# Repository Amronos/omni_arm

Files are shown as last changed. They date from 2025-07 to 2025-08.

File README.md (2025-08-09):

# Omni Arm

**_This is a work in progress and not usable currently._**

A universal robot arm featuring 3 robot grippers (parallel jaw, suction cup, and jamming) and 9 DOFS (including 3 for each gripper), allowing it to pickup objects of any kind as long as they have reasonable size and weight.

## Features

- 1 DOF for rotation on the x-axis.
- 3 DOFs for rotation on the y-axis.
- 2 DOFs for rotation on the z-axis.
- 3 different grippers: parallel jaw, suction cup, and jamming.
- Can pickup objects of any kind as long as they are of reasonable weight and size (size is not a limit for the suction cup gripper).
- Precise arm position control alongside position, velocity, load, and input voltage feedback from Waveshare servo motors.
- [ROS 2](https://docs.ros.org) support that uses [MoveIt 2](https://moveit.ai). (Coming Soon)

## Why Create This?

There are hardly any open-source and low-cost robot arms available out there that allow you to pikcup all sorts of objects with the use of various grippers.<br>
Most of the avilable robot arms also don't offer the kind of feedback and control one needs on the motors to perform complex kinematics and dynamics.<br>
This robot arm does all of that, making it perfect for my use-cases.

## Images

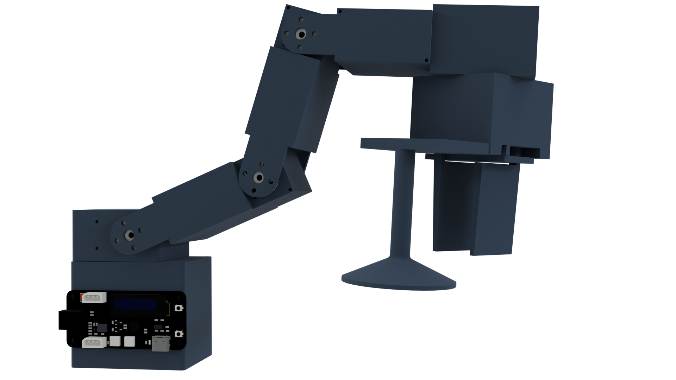
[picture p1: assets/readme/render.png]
Render

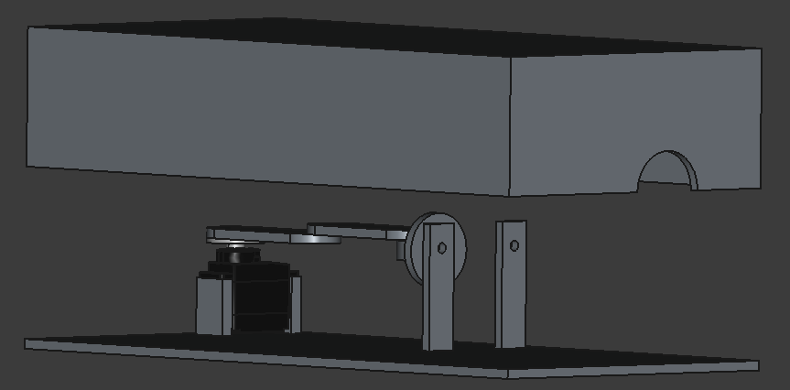
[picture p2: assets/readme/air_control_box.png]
Air Control Box

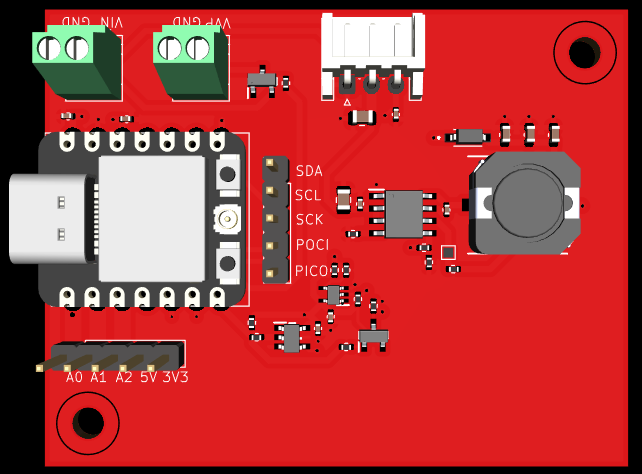
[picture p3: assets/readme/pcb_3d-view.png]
PCB 3D View


## Wiring Diagram

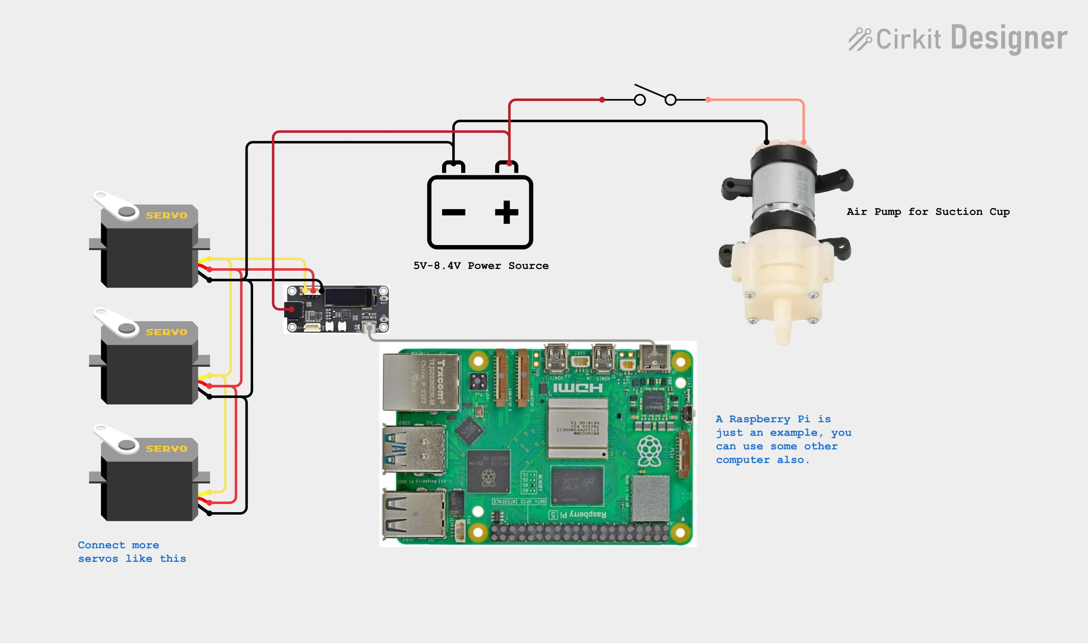
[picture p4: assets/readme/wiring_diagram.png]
Wiring Diagram


## BOM

| Item | Unit Price | Quantity | Total Price | Links |
| --- | --- | --- | --- | --- |
| Waveshare SC15 Servo | $17.99 | 4 | $71.96 | https://www.waveshare.com/sc15-servo.htm |
| Waveshare SC09 Servo | $8.99 | 4 | $35.96 | https://www.waveshare.com/sc09-servo.htm |
| PCB | $43.77 | 2 | $43.77 | https://jlpcb.com/ |
| Xiao ESP32-C3 | $5.71 | 1 | $5.71 | https://thinkrobotics.com/products/seeed-studio-xiao-esp32c3 |
| Dispo Van 20 ml Plastic Syringe | $0.23 | 1 | $0.23 | https://www.amazon.in/DISPO-Plastic-Syringe-Medical-Purpose/dp/B09KS18BMY |
| Suction Cup Gripper for DIY Robot Arms  | $27.85 | 1 | $27.85 | https://thinkrobotics.com/products/suction-cup-gripper-for-diy-robot-arms |
| M2x9.5 Pan Head Self Tapping Screw | — | 10 | — | — |
| M2x6.5 Pan Head Self Tapping Screw | — | 10 | — | — |
| M3x8 Pan Head Self Tapping Screw | — | 4 | — | — |
| M3x10 Pan Head Self Tapping Screw | — | 2 | — | — |
| 2x50mm Stainless Steel Round Shaft Rods | — | 2 | — | — |
| 3D Prints | — | 1 | — | https://github.com/Amronos/omni_arm/tree/main/CAD |
| | | | $185.48 | |

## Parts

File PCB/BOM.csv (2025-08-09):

Designator | Quantity | Value | Footprint | Manufacturer | Mfr. Part No. | JLCPCB Part #
C1, C12 | 2 | 10 µF | C_0805_2012Metric | Murata Electronics | GRM21BR61H106KE43L | C440198
C10, C2, C3, C7, C8, C9 | 6 | 100 nF | C_0402_1005Metric | Samsung Electro-Mechanics | CL05B104KB54PNC | C307331
C11 | 1 | 470 pF | C_0402_1005Metric | Murata Electronics | GCM155R72A471KA37D | C464449
C4, C5, C6 | 3 | 22 µF | C_0603_1608Metric | Murata Electronics | GRT188R61A226ME13D | C126630
D1 | 1 | 1N5819HW-7-F | SOD3715X145N | Diodes Incorporated | 1N5819HW-7-F | C82544
J1, J4 | 2 | Screw_Terminal_01x02 | TerminalBlock_Xinya_XY308-2.54-2P_1x02_P2.54mm_Horizontal | Ningbo Xinlaiya Elec. | XY308-2.54-2P | C557685
J2, J3 | 2 | Conn_01x05 | PinHeader_1x05_P2.54mm_Vertical | Generic | Generic
J5 | 1 | Conn_01x03 | JST_EH_S3B-EH_1x03_P2.50mm_Horizontal | BOOMELE(Boom Precision Elec) | 5264-3A | C146133
L1 | 1 | 15 µH | INDPM102100X400N | Coilcraft | MSS1038-153MLC | C18212714
Q1, Q2 | 2 | MMBT3906LT3G | SOT96P237X111-3N | Onsemi | MMBT3906LT3G | C232602
R1, R10, R11, R13, R3, R4, R9 | 7 | 10 kΩ | R_0402_1005Metric | Panasonic Electronic Components | ERA-2AEB103X | C191915
R6 | 1 | 64.9 kΩ | R_0402_1005Metric | Panasonic Electronic Components | ERA-2AEB6492X | C490835
R7 | 1 | 100 kΩ | R_0402_1005Metric | Panasonic Electronic Components | ERA-2AEB104X | C445619
R8 | 1 | 24.9 kΩ | R_0402_1005Metric | Panasonic Electronic Components | ERA-2AEB2492X | C490822
U1 | 1 | MOUDLE-SEEEDUINO-XIAO-ESP32C3 | XIAO-ESP32C3-SMD | Seeed Studio | XIAO ESP32C3
U3 | 1 | LMR38020FDDAR | SOIC127P600X170-9N | Texas Instruments | LMR38020FDDAR | C5149193
U4 | 1 | SN74LVC1G126DBVR | SOT95P280X145-5N | Texas Instruments | SN74LVC1G126DBVR | C7834
U5 | 1 | SN74LVC1G125DCKR | SOT65P210X110-5N | Texas Instruments | SN74LVC1G125DCKR | C7833

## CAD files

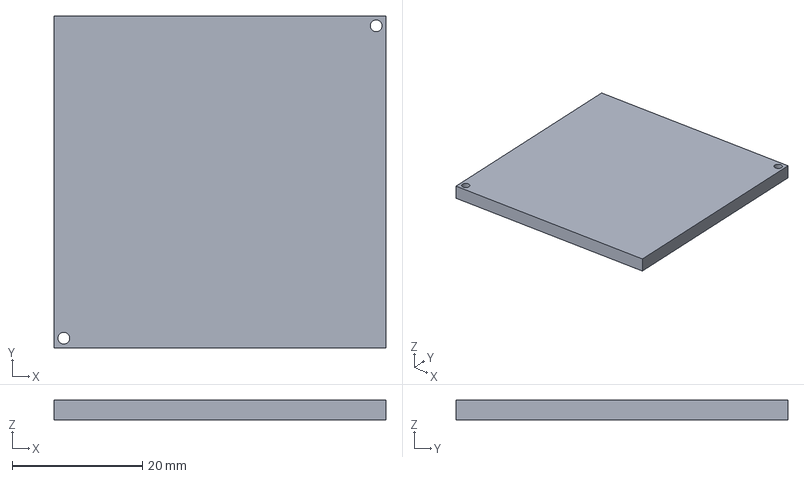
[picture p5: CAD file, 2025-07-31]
CAD/Z-Axis_2_Front.step
50.9 x 50.9 x 3.00 mm

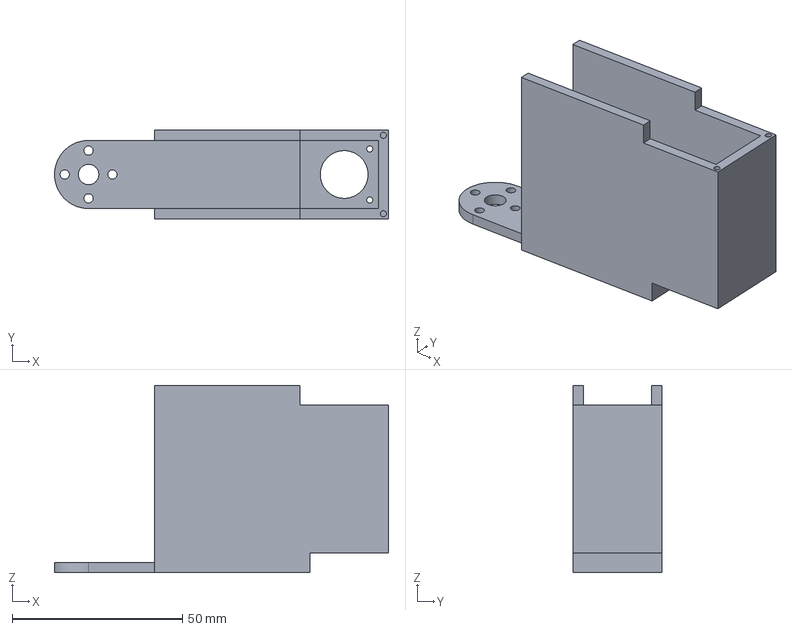
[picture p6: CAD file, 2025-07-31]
CAD/Y-Axis_2_Left.step
98.0 x 26.0 x 54.9 mm

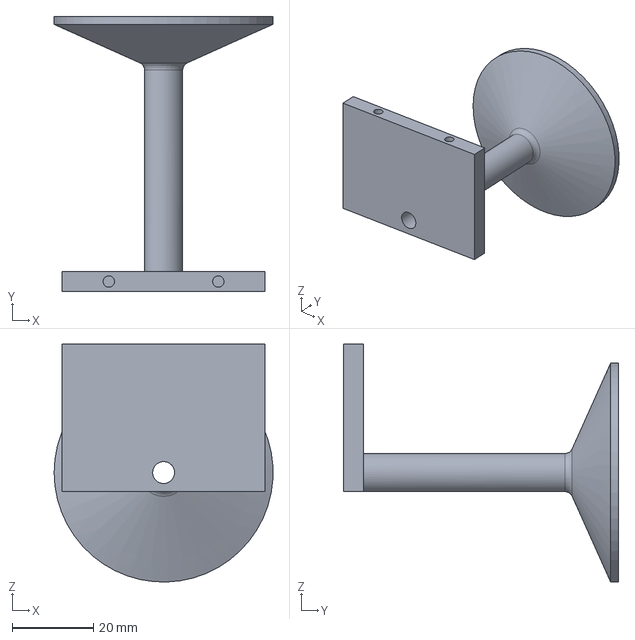
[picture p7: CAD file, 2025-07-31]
CAD/Jamming_Gripper_Funnel.step
53.9 x 67.9 x 58.7 mm

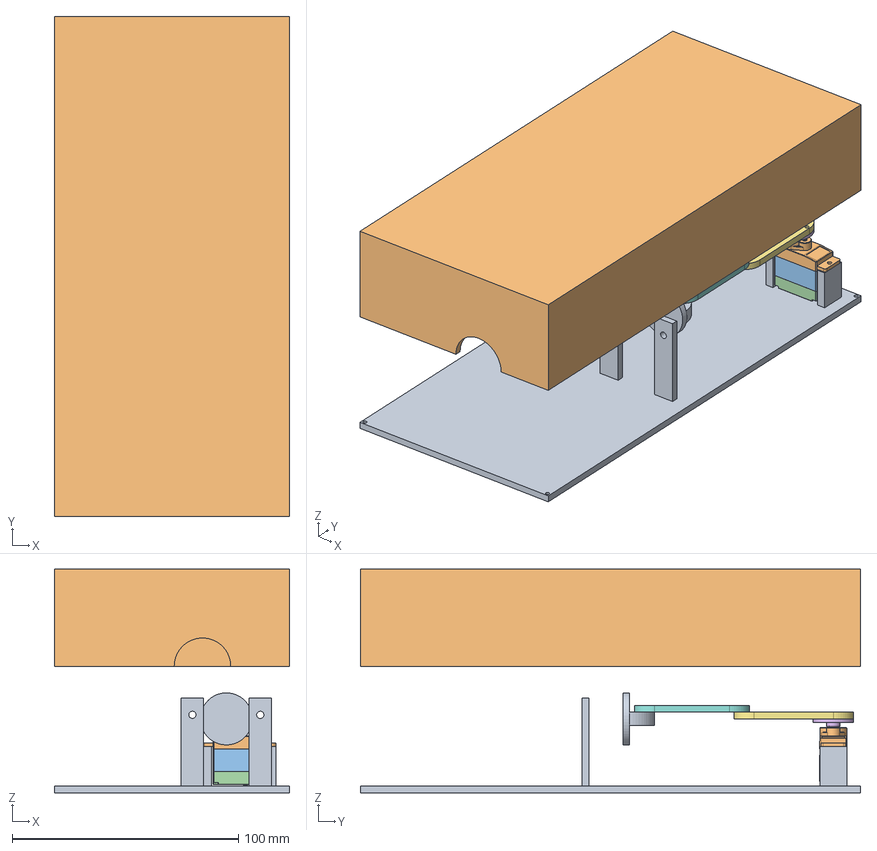
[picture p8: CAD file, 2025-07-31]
CAD/air_control_box.FCStd
104.0 x 221.0 x 99.0 mm
Base
SJ-WK00-0038-TOPCASE-0716_41_1
SJ-WK00-0039-COREMIDDLE-0716_65
SJ-WK00-0037-BOTTOMCASE-0716_9_
SJ-CL00-0027-OUTPUTGEAR-0716_37
SC09_Horn
Syringe_Connector
Cover

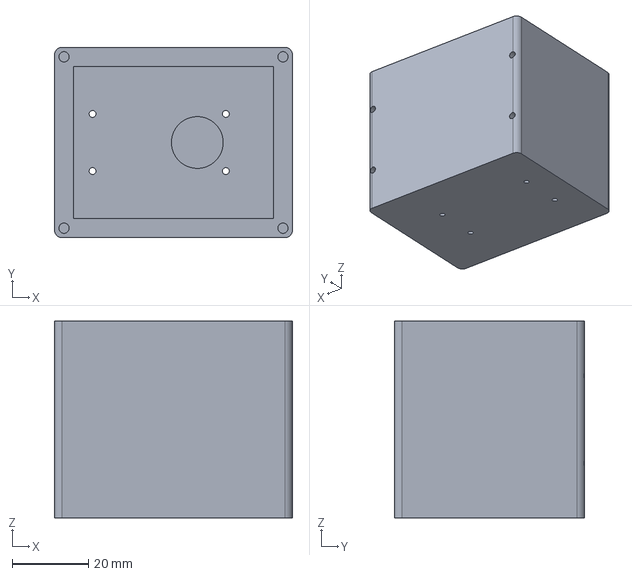
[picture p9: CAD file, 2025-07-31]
CAD/Z-Axis_Base.step
62.5 x 50.0 x 51.7 mm

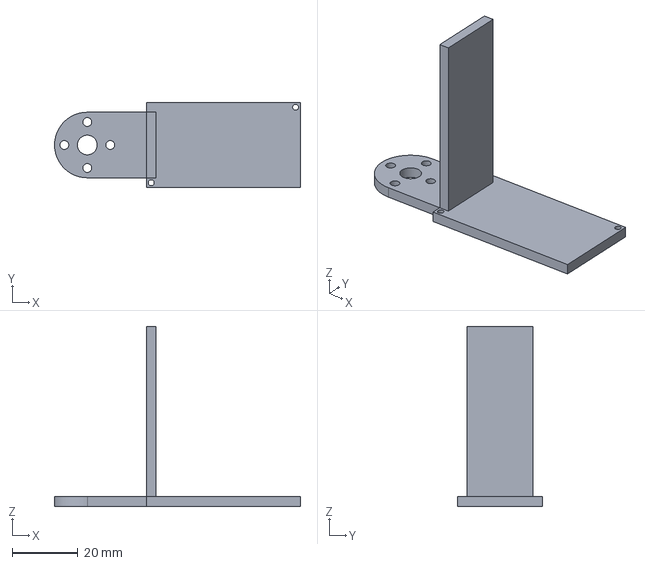
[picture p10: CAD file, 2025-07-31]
CAD/X-Axis_Right.step
75.0 x 26.0 x 54.9 mm

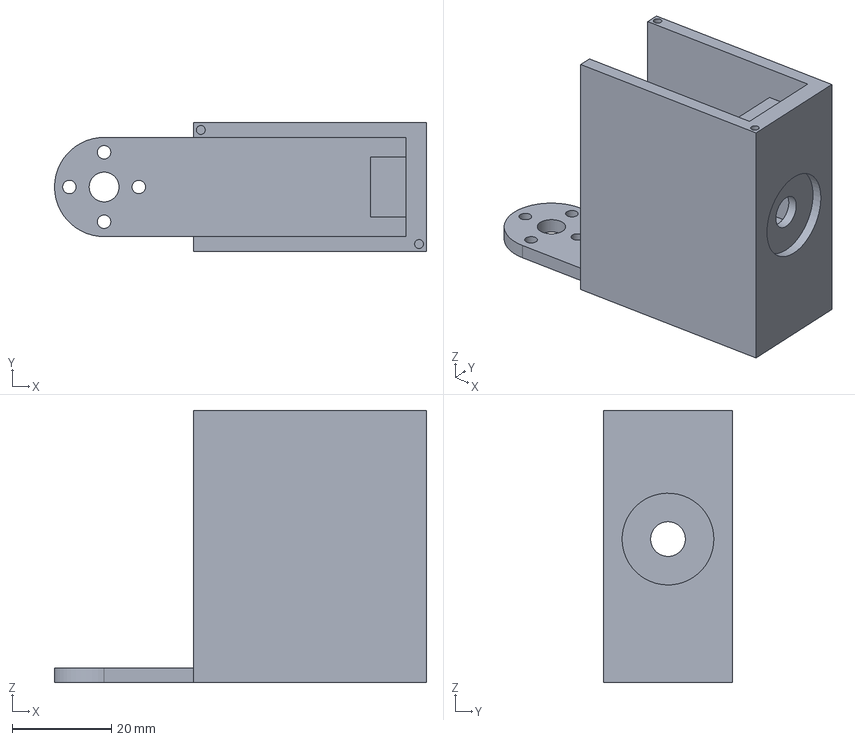
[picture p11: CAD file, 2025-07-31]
CAD/X-Axis_Left.step
75.0 x 26.0 x 54.9 mm

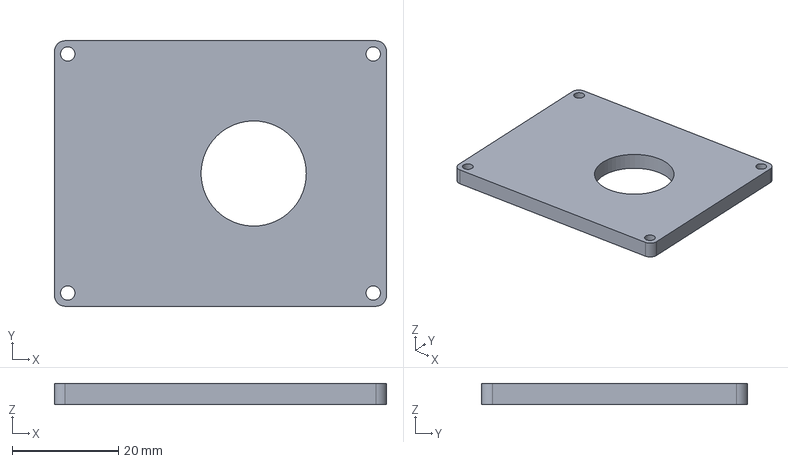
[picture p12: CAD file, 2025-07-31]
CAD/Z-Axis_Lid.step
62.5 x 50.0 x 3.98 mm

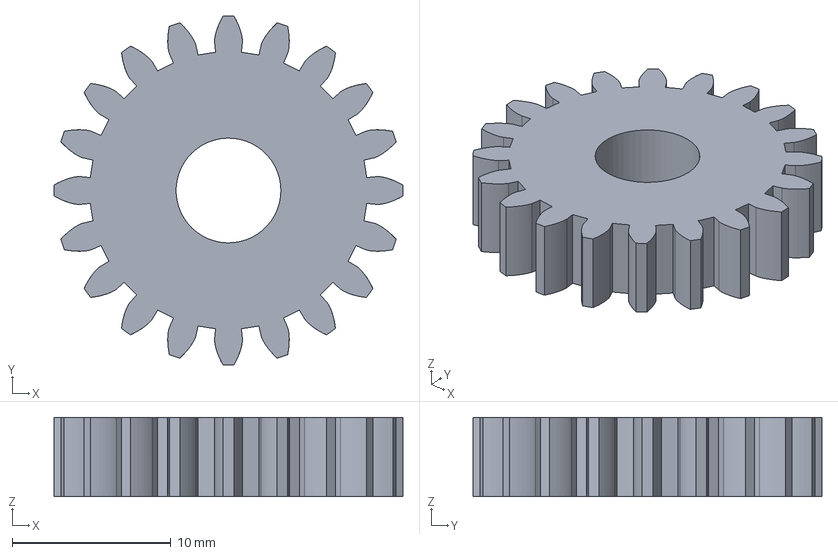
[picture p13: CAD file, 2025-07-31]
CAD/Parallel_Gripper_Part_3.step
22.0 x 22.0 x 5.00 mm

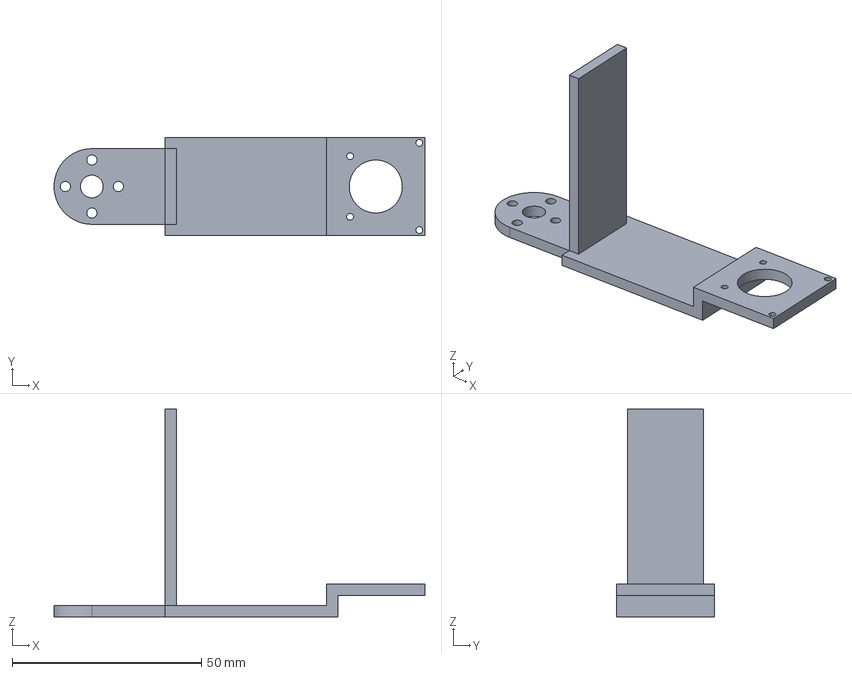
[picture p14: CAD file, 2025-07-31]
CAD/Y-Axis_2_Right.step
98.0 x 26.0 x 54.9 mm

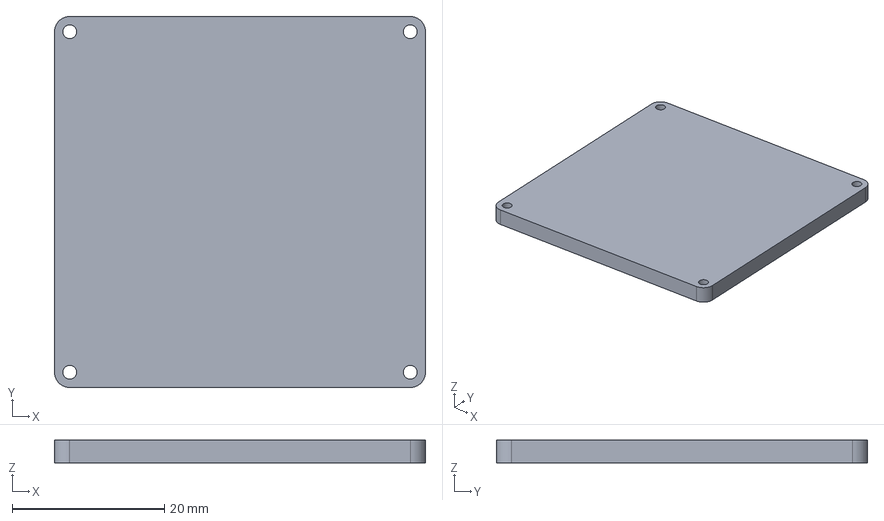
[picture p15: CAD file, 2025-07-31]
CAD/Y-Axis_Lid.step
48.7 x 48.7 x 3.00 mm

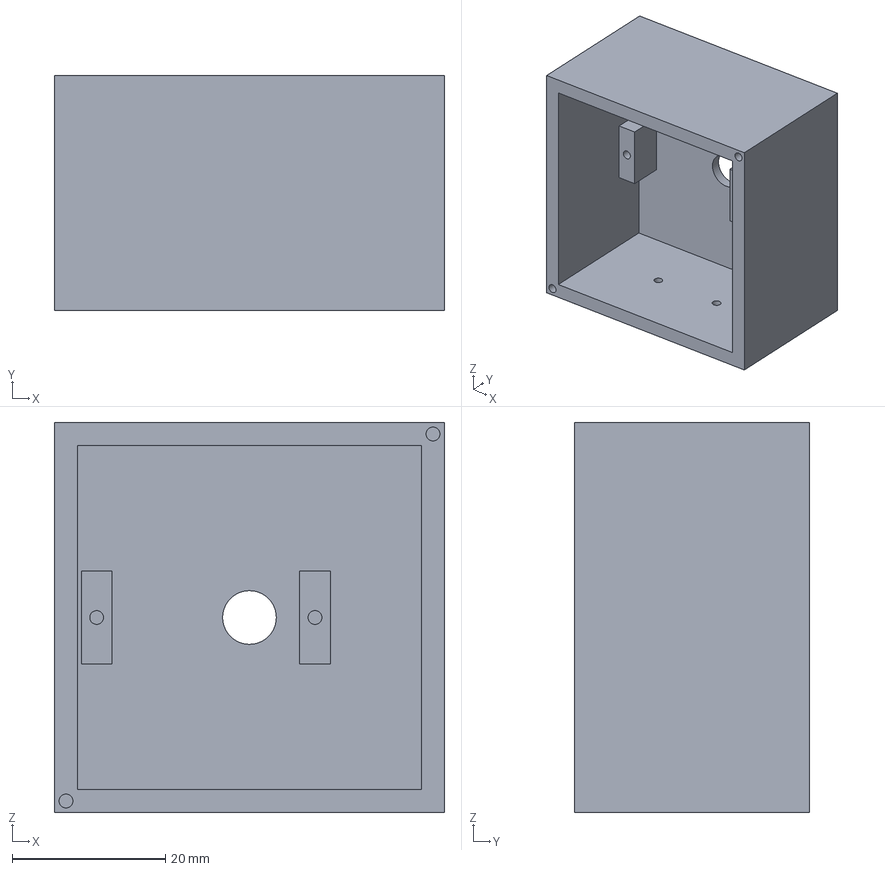
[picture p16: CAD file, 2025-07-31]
CAD/Z-Axis_2_Back.step
50.9 x 30.6 x 50.9 mm

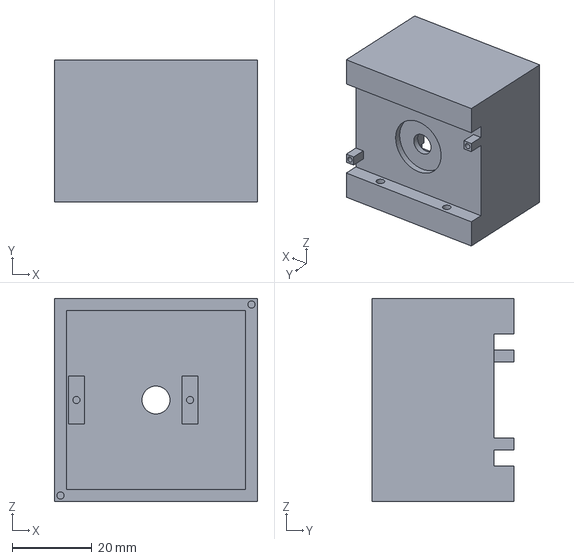
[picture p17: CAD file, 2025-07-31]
CAD/Parallel_Gripper_Part_1.step
50.9 x 35.6 x 50.9 mm

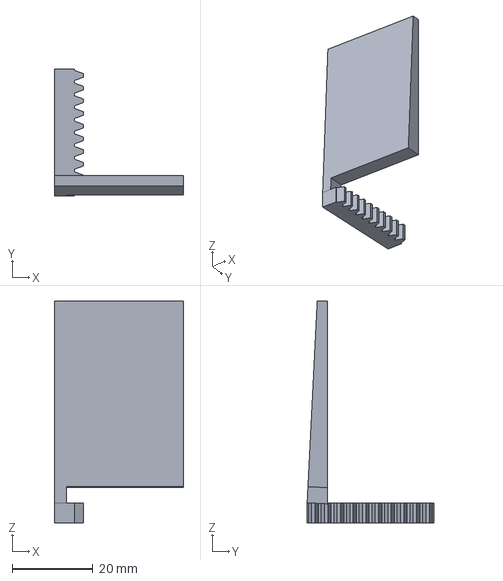
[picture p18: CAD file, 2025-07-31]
CAD/Parallel_Gripper_Part_4.step
32.0 x 31.4 x 55.0 mm

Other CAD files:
CAD/Parallel_Gripper_Part_2.step
CAD/Parallel_Gripper_Part_5.step
CAD/Y-Axis_Base.step
CAD/omni_arm.FCStd

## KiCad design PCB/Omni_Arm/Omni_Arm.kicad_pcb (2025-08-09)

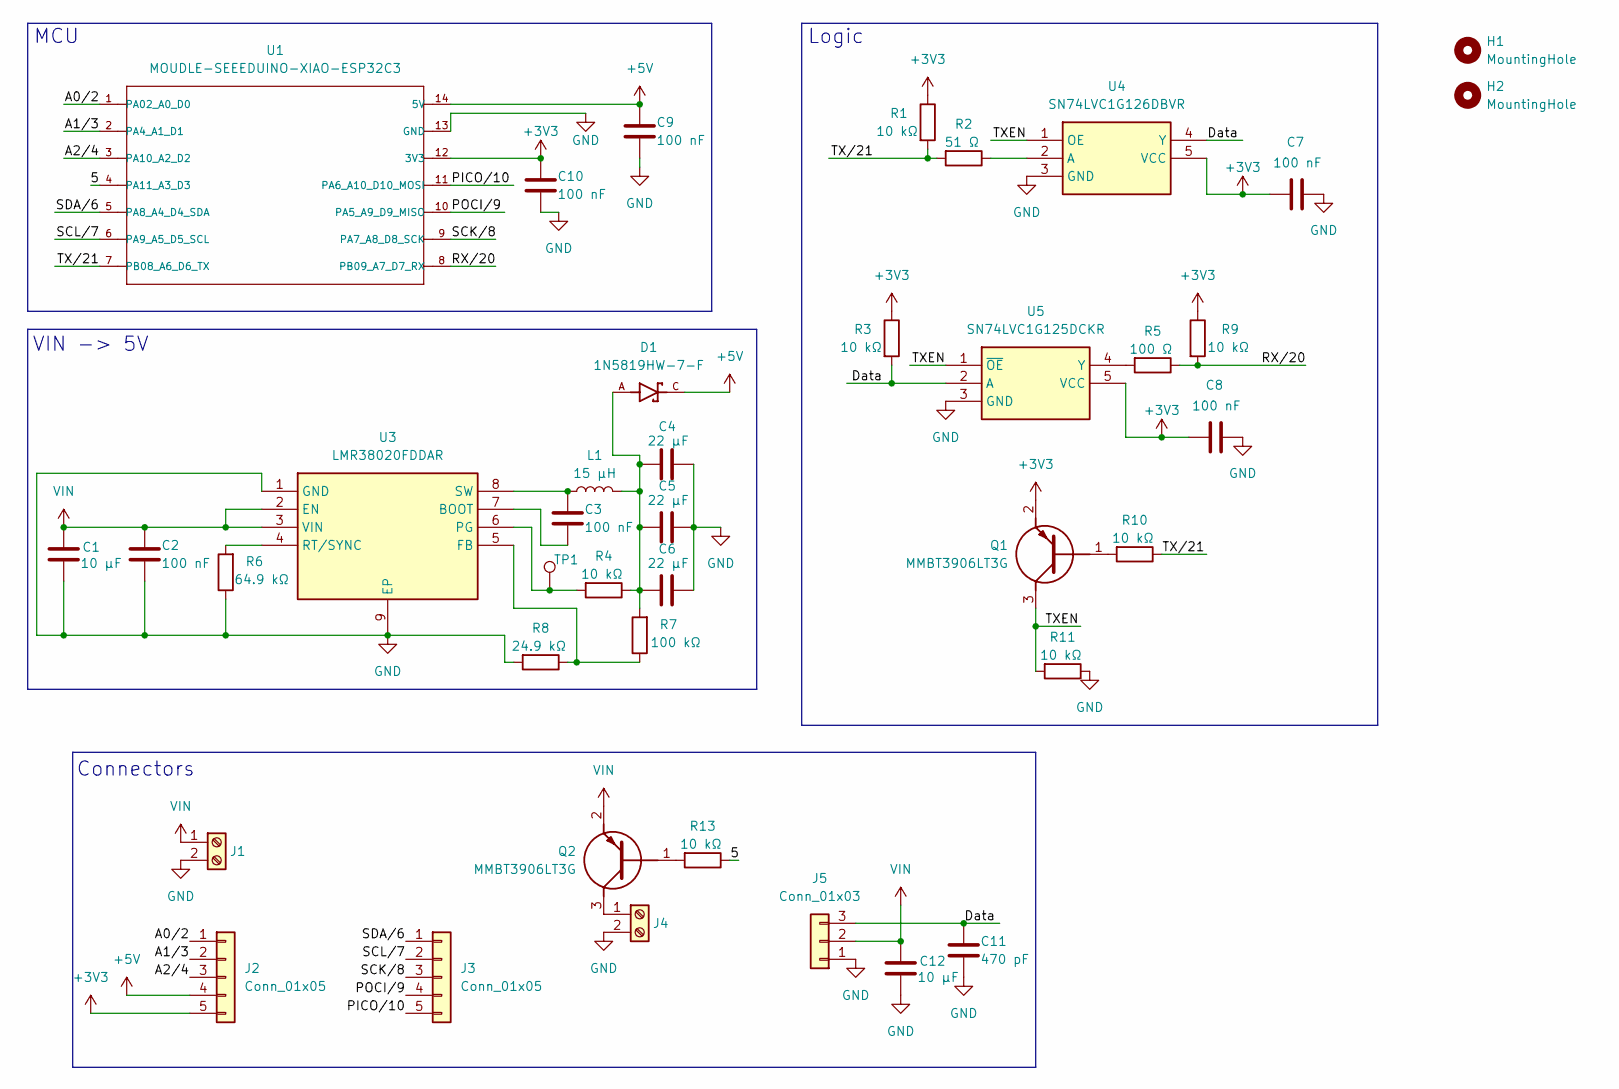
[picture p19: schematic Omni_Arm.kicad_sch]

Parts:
C1, C12: 10 µF; C_0805_2012Metric
C2, C3, C7, C8, C9, C10: 100 nF; C_0402_1005Metric
C4, C5, C6: 22 µF; C_0603_1608Metric
C11: 470 pF; C_0402_1005Metric
D1: 1N5819HW-7-F; SOD3715X145N
H1, H2: MountingHole; MountingHole_3.2mm_M3
J1, J4: Screw_Terminal_01x02; TerminalBlock_Xinya_XY308-2.54-2P_1x02_P2.54mm_Horizontal
J2, J3: Conn_01x05; PinHeader_1x05_P2.54mm_Vertical
J5: Conn_01x03; JST_EH_S3B-EH_1x03_P2.50mm_Horizontal
L1: 15 µH; INDPM102100X400N
Q1, Q2: MMBT3906LT3G; SOT96P237X111-3N; Mouser Part Number 863-MMBT3906LT3G
R1, R3, R4, R9, R10, R11, R13: 10 kΩ; R_0402_1005Metric
R2: 51 Ω; R_0402_1005Metric
R5: 100 Ω; R_0402_1005Metric
R6: 64.9 kΩ; R_0402_1005Metric
R7: 100 kΩ; R_0402_1005Metric
R8: 24.9 kΩ; R_0402_1005Metric
TP1: TestPoint; TestPoint_Pad_1.0x1.0mm
U1: MOUDLE-SEEEDUINO-XIAO-ESP32C3; XIAO-ESP32C3-SMD
U3: LMR38020FDDAR; SOIC127P600X170-9N
U4: SN74LVC1G126DBVR; SOT95P280X145-5N; Manufacturer_Part_Number SN74LVC1G126DBVR; Mouser Part Number 595-SN74LVC1G126DBVR
U5: SN74LVC1G125DCKR; SOT65P210X110-5N; Manufacturer_Part_Number SN74LVC1G125DCKR; Mouser Part Number 595-SN74LVC1G125DCKR

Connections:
+3V3: C7.1, C8.1, C10.1, J2.5, Q1.2 (E), R1.1, R3.1, R9.1, U1.12 (3V3), U4.5 (VCC), U5.5 (VCC)
+5V: C9.1, D1.C, J2.4, U1.14 (5V)
/5: R13.1, U1.4 (PA11_A3_D3)
/A0/2: J2.1, U1.1 (PA02_A0_D0)
/A1/3: J2.2, U1.2 (PA4_A1_D1)
/A2/4: J2.3, U1.3 (PA10_A2_D2)
/Data: C11.1, J5.3, R3.2, U4.4 (Y), U5.2 (A)
/PICO/10: J3.5, U1.11 (PA6_A10_D10_MOSI)
/POCI/9: J3.4, U1.10 (PA5_A9_D9_MISO)
/RX/20: R5.1, R9.2, U1.8 (PB09_A7_D7_RX)
/SCK/8: J3.3, U1.9 (PA7_A8_D8_SCK)
/SCL/7: J3.2, U1.6 (PA9_A5_D5_SCL)
/SDA/6: J3.1, U1.5 (PA8_A4_D4_SDA)
/TXEN: Q1.3 (C), R11.2, U4.1 (OE), U5.1 (~OE)
/TX/21: R1.2, R2.2, R10.1, U1.7 (PB08_A6_D6_TX)
GND: C1.2, C2.2, C4.2, C5.2, C6.2, C7.2, C8.2, C9.2, C10.2, C11.2, C12.2, J1.2, J4.2, J5.1, R6.1, R8.2, R11.1, U1.13 (GND), U3.1 (GND), U3.9 (EP), U4.3 (GND), U5.3 (GND)
unnamed: C4.1, C5.1, C6.1, D1.A, L1.2, R4.1, R7.2
unnamed: J4.1, Q2.3 (C)
unnamed: Q1.1 (B), R10.2
unnamed: Q2.1 (B), R13.2
unnamed: C3.2, U3.7 (BOOT)
unnamed: R7.1, R8.1, U3.5 (FB)
unnamed: R4.2, TP1.1, U3.6 (PG)
unnamed: R6.2, U3.4 (RT/SYNC)
unnamed: C3.1, L1.1, U3.8 (SW)
unnamed: R2.1, U4.2 (A)
unnamed: R5.2, U5.4 (Y)
VIN: C1.1, C2.1, C12.1, J1.1, J5.2, Q2.2 (E), U3.2 (EN), U3.3 (VIN)

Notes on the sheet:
Logic
VIN -> 5V
Connectors
MCU

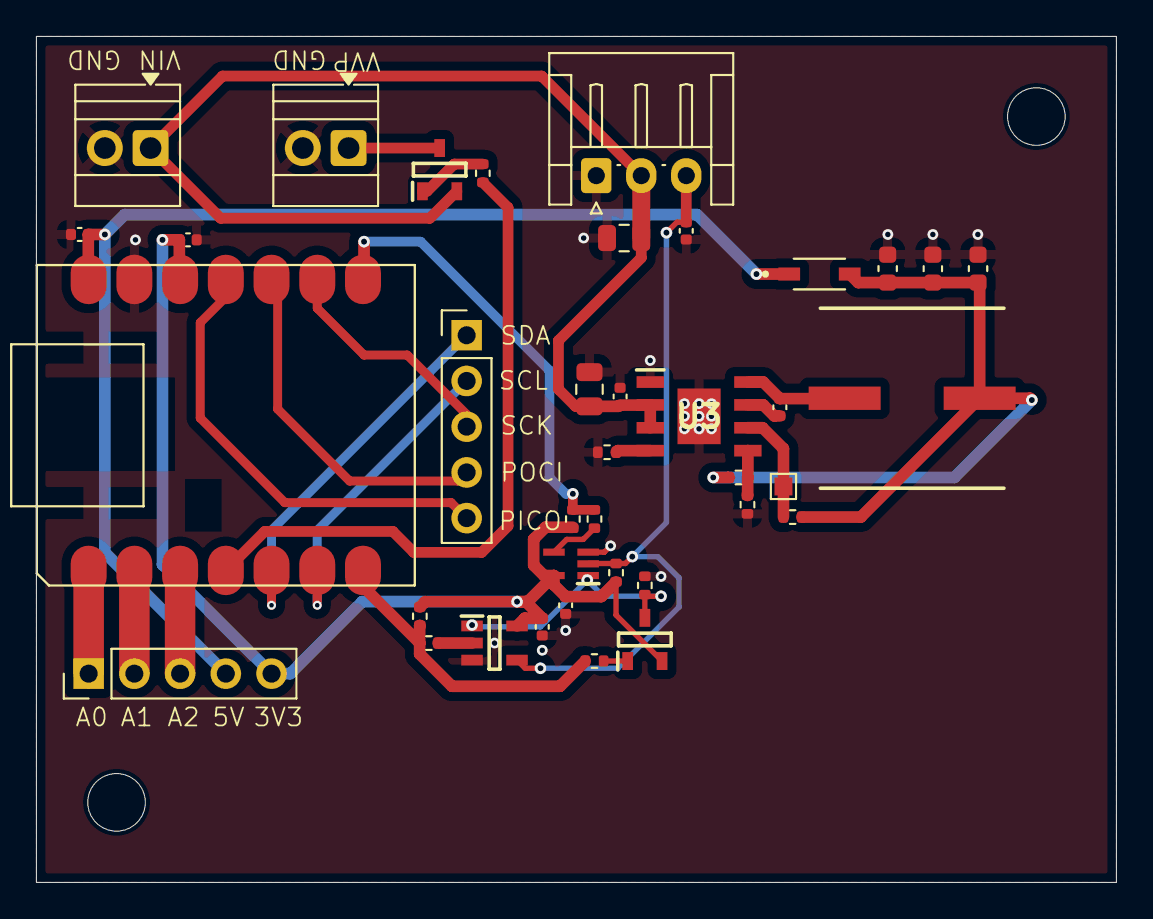
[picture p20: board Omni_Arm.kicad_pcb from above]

Board: 2 copper layers, 60.0 x 47.0 mm, 40 parts (0 on the bottom side), 28 nets.

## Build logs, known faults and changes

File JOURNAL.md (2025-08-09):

---
title: "Omni Arm"
author: "Aarav Gupta"
description: "A unviersal robot arm featuring 3 robot grippers (parallel jaw, suction cup, and jamming) and 9 DOFS."
created_at: "2025-07-8"
total_time_spent: 51 hours
---

## 6th to 8th August 2025: Created a Custom PCB

I still haven't printed the arm, but decided to create a PCB for that so that I can control the suction cup, gripper from the MCU directly, instead of manually operating a switch. (I haven't explicitly mentioned this in the journal before, but this was the case.)<br>
The PCB uses a Xiao ESP32-C3 and can control serial bus servo motors. Therefore, the Waveshare Servo Driver is no longer needed.<br>
To create this PCB I first spent some time looking at commercially availabe serial bus servo motor drivers, after taking inspiration from them I started to design my own.<br>
I then spent some time changing the 3D model of the arm to support the new PCB instead of the previous servo driver, alongside working on the BOM for the PCB and the BOM for the entire project.

| 3D View | Schematic Diagram |
| :---: | :---: |
| 3D View | Schematic Diagram |

**Total time spent: 7h**

## 30th to 31st July 2025: Ready for First Print

I spent these two days completing the jamming gripper and making the air control box (houses the syringe, it's servo motor, and electronics for the suction cup). This project is ready to be printed and tested now!<br>
I haven't made any special mounting for the parts for the suction cup gripper for this first print (I don't know their exact measurements yet), for now they will be hot-glued to the arm / air-control box.<br>
I also completed the first basic version of the firmware and made a wiring diagram.

| Render of the Arm | Air Control Box |
| :---: | :---: |
| Render of the Arm | Air Control Box |

**Total time spent: 10.5h**

## 28th to 29th July 2025: Complete Parallel Gripper

I spent these two days completing the parallel gripper, I used a rack and pinion design for it.<br>
By moving the arm in assembly, I found that the arm would face difficult picking up objects that are near it, when using the suction cup or jamming gripper. To fix this I have added another DOF on the Y-Axis.

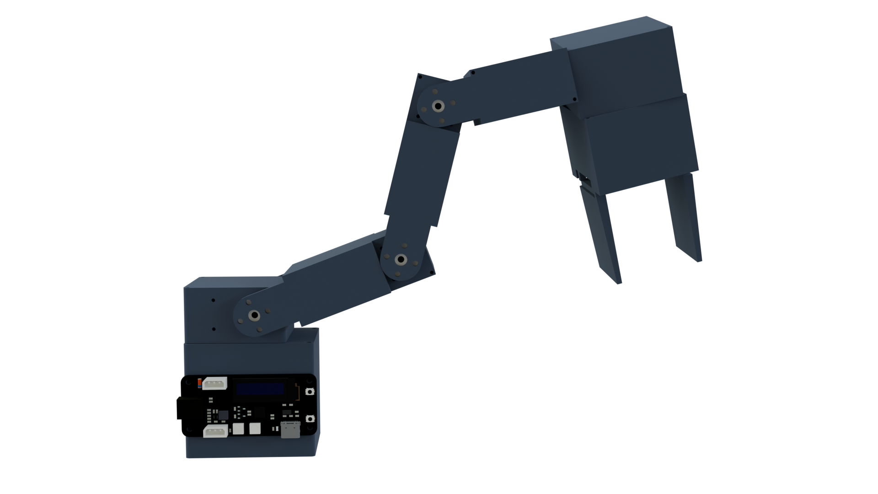
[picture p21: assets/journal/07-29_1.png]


**Total time spent: 7.5h**

## 27th July 2025: Complete X-Axis_2

Today IP completed the housing for the second motor which allows rotation on the z-axis. This one is near the grippers, and is for switching between them.

**Total time spent: 3h**

## 26th July 2025: Complete X-Axis

Today I completed the housing for the motor that allows rotation on the x-axis and spent a few hours trying to figure out how to render my model.

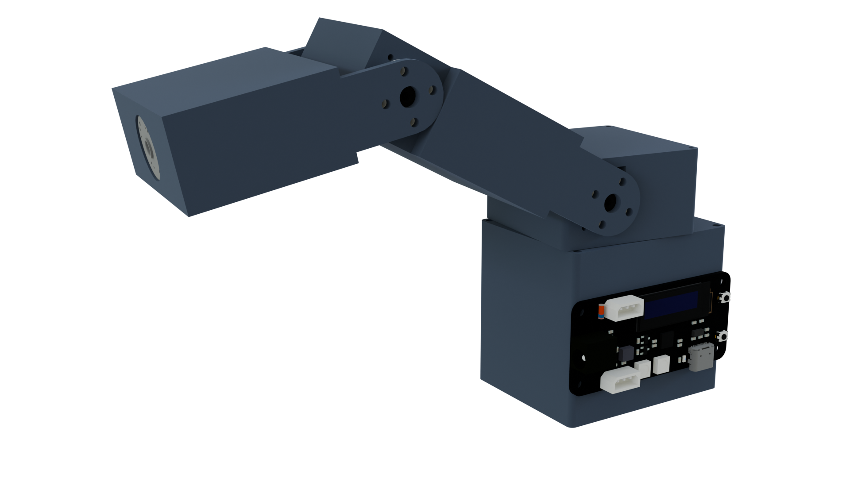
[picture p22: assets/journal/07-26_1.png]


**Total time spent: 5h**

## 19th to 25th July 2025: Complete Y-Axis_2

I spent these days working on the second motor for rotation on the y-axis.<br>
I had to many times measure the servo motor's dimensions, check how everything appeared in the assembly, and according fix things in my model.<br>
I have gotten better at designing for these servo motors, and so I am thinking of updating the design for the first y-axis motor.

**Total time spent: 7h**

## 19th July 2025: Changed the Idea a Bit

Today I decided to change the idea of the project a bit, it will now be called Omni Arm and have 8 DOFs (including 3 for 3 different grippers).<br>
There will be 3 different grippers: parallel jaw, suction cup, and jamming. The suction cup will be controlled through a vacuum pump, parallel jaw gripper through an [SC09 Servo](https://www.waveshare.com/sc09-servo.htm), and the jamming gripper through a syringe and an [SC09 Servo](https://www.waveshare.com/sc09-servo.htm).<br>
Close to the grippers there will be 2 [SC09 Servo](https://www.waveshare.com/sc09-servo.htm) one for switching between the grippers (z-axis rotation) and one for x-axis rotation (as before).<br>
The rest says the same (2 DOFs for rotation on the z-axis and y-axis that will use [SC15 Servos](https://www.waveshare.com/sc15-servo.htm)) except for an additional y-axis DOF in the arm which will use the [SC15 Servo](https://www.waveshare.com/sc15-servo.htm).

**Total time spent: 3h**

## 13th to 18th July 2025: Complete Y-Axis Housing

I spent these days reworking/creating the housing for the y-axis motor, considering various shapes and sizes for the design. I ended up going with a simple cubic housing.<br>
I also researched into what syringe to use and the servo motor controlling it will be placed in the arm. Since there were no small syringes which could offer the volume of air I wanted (~20ml), I decided to create a completely separate assembly for it.

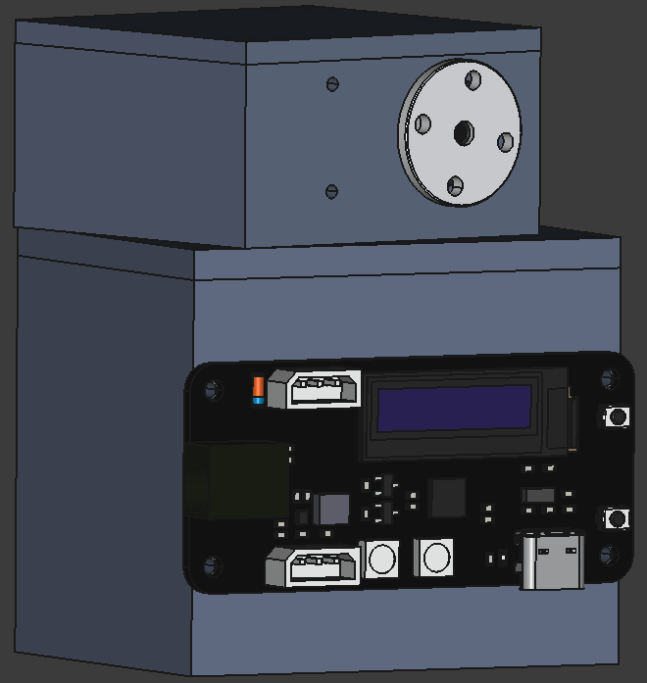
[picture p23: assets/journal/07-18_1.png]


**Total time spent: 7.5h**

## 11th to 12th July 2025: Complete Base

During these two days I completed 3D modelling the base of the gripper which houses the z-axis motor and to which the servo driver is attached.<br>
I also created the rotational base for the y-axis motor that is attached to the z-axis motor.

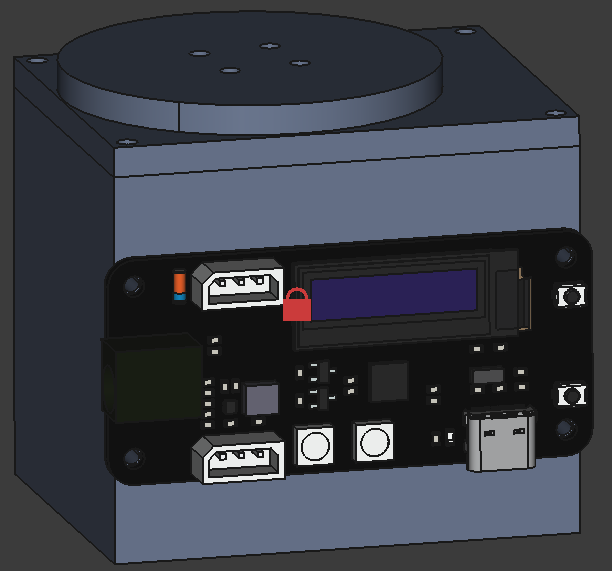
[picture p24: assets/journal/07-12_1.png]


**Total time spent: 5h**

## 8th to 10th July 2025: Initial Research

I spent these days researching into different motors, vacuum pumps, and robot arms.<br>
I decided that the gripper will have 4 DOFs, 1 each for angular movement on all 3 axes (x, y, and z) and 1 for controlling the air pressure in the end effector. I will use the [SC15 Servo](https://www.waveshare.com/sc15-servo.htm) for rotation on the z and y axes, and the [SC09 Servo](https://www.waveshare.com/sc09-servo.htm) for the x axis and end-effector.<br>
I also worked on the base of the gripper on 10th July (today), adding mounting screw holes for the z-axis motor.

**Total time spent: 6h**

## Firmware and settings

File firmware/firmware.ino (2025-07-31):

/*
  Commands for control over Serial/UART:
  - m <ID> <position>: Move servo to a raw position value (0-1023).
  - d <ID> <degrees>: Move servo to a degree value (0-300).
  - f <ID>: Get all feedback for a servo (Position, Speed, Load, Voltage, Temperature).
  - p <ID>: Get position of a servo.
  - s <ID>: Get speed of a servo.
  - l <ID>: Get load of a servo.
  - v <ID>: Get voltage of a servo.
  - t <ID>: Get temperature of a servo.

  Example: "d 1 90" will move servo with ID 1 to 90 degrees.
*/

// The UART used to control servos.
#define S_RXD 18
#define S_TXD 19

#include <SCServo.h>

SCSCL sc;

// Command parsing variables
char cmd;
char argv1[16];
char argv2[16];
long arg1;
long arg2;
int arg_index = 0;
int char_index = 0;

void setup() {
  Serial.begin(115200);
  Serial1.begin(1000000, SERIAL_8N1, S_RXD, S_TXD);
  sc.pSerial = &Serial1;
  delay(1000);
}

void loop() {
  while (Serial.available() > 0) {
    char chr = Serial.read();

    if (chr == '\r') {
      if (arg_index == 1) argv1[char_index] = '\0';
      else if (arg_index == 2) argv2[char_index] = '\0';
      runCommand();
      resetCommand();
    } else if (chr == ' ') {
      if (arg_index == 0) arg_index = 1;
      else if (arg_index == 1) {
        argv1[char_index] = '\0';
        arg_index = 2;
        char_index = 0;
      }
    } else {
      if (arg_index == 0) {
        cmd = chr;
      } else if (arg_index == 1) {
        argv1[char_index] = chr;
        char_index++;
      } else if (arg_index == 2) {
        argv2[char_index] = chr;
        char_index++;
      }
    }
  }
}

void resetCommand() {
  cmd = '\0';
  memset(argv1, 0, sizeof(argv1));
  memset(argv2, 0, sizeof(argv2));
  arg1 = 0;
  arg2 = 0;
  arg_index = 0;
  char_index = 0;
}

void runCommand() {
  arg1 = atoi(argv1);
  arg2 = atoi(argv2);

  switch (cmd) {
    case 'm':
      moveServo(arg1, arg2);
      break;
    case 'd':
      moveServoDegrees(arg1, arg2);
      break;
    case 'f':
      getFeedback(arg1);
      break;
    case 'p':
      getPosition(arg1);
      break;
    case 's':
      getSpeed(arg1);
      break;
    case 'l':
      getLoad(arg1);
      break;
    case 'v':
      getVoltage(arg1);
      break;
    case 't':
      getTemperature(arg1);
      break;
    default:
      Serial.println("Invalid Command");
      break;
  }
}

void moveServo(int id, int position) {
  sc.WritePos(id, position, 0, 1500); // Using default speed
  Serial.println("OK");
}

void moveServoDegrees(int id, int degrees) {
  int position = map(degrees, 0, 300, 0, 1023); // Assuming 300-degree servo
  sc.WritePos(id, position, 0, 1500);
  Serial.println("OK");
}

void getFeedback(int id) {
  if (sc.FeedBack(id) != -1) {
    Serial.print(sc.ReadPos(-1));
    Serial.print(" ");
    Serial.print(sc.ReadSpeed(-1));
    Serial.print(" ");
    Serial.print(sc.ReadLoad(-1));
    Serial.print(" ");
    Serial.print(sc.ReadVoltage(-1));
    Serial.print(" ");
    Serial.println(sc.ReadTemper(-1));
  } else {
    Serial.println("Error");
  }
}

void getPosition(int id) {
  int pos = sc.ReadPos(id);
  if (pos != -1) {
    Serial.println(pos);
  } else {
    Serial.println("Error");
  }
}

void getSpeed(int id) {
  int speed = sc.ReadSpeed(id);
  if (speed != -1) {
    Serial.println(speed);
  } else {
    Serial.println("Error");
  }
}

void getLoad(int id) {
  int load = sc.ReadLoad(id);
  if (load != -1) {
    Serial.println(load);
  } else {
    Serial.println("Error");
  }
}

void getVoltage(int id) {
  int voltage = sc.ReadVoltage(id);
  if (voltage != -1) {
    Serial.println(voltage);
  } else {
    Serial.println("Error");
  }
}

void getTemperature(int id) {
  int temp = sc.ReadTemper(id);
  if (temp != -1) {
    Serial.println(temp);
  } else {
    Serial.println("Error");
  }
}

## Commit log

2025-07-10 Add z-axis servo motor
    [BOM.csv, omninado_gripper.FCStd]
2025-07-13 Complete base
    [BOM.csv, omninado_gripper.FCStd]
2025-07-18 Complete housing for y-axis motor
    [BOM.csv, omninado_gripper.FCStd]
2025-07-19 Change the idea a bit
    [BOM.csv, omni_arm.FCStd]
2025-07-26 Complete Y-Axis_2
2025-07-27 Complete housing for x-axis motor
2025-07-27 Complete housing for Z-Axis_2
2025-07-30 Complete parallel gripper and add another y-axis DOF
    [BOM.csv]
2025-07-31 Complete 3D model for printing and update README.md
    [BOM.csv, Jamming_Gripper_Funnel.step, Parallel_Gripper_Part_1.step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]
2025-07-31 Add firmware and wiring diagram
2025-08-09 Add custom PCB
    [BOM.csv, Omni_Arm.kicad_pcb, Omni_Arm.kicad_sch]
2025-08-09 Fix BOM and path
    [BOM.csv]
